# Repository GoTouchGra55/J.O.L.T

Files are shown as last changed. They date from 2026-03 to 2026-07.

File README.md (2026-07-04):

# 🚧 Under Active Development 🚧

# J.O.L.T ⚡

## Overview

JOLT (short for Joint Operated Legged Terrain walker) is my attempt at making a 12-DOF quadruped robot from scratch.

Yes, I designed a custom STM32-based dev board, CAD, and will implement custom firmware! :3

---

### PCB Design (2-layer)

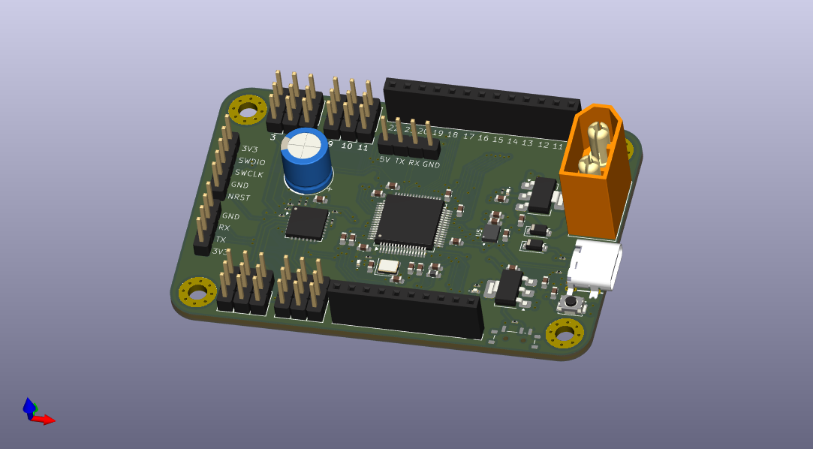
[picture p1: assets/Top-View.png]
PCB Top


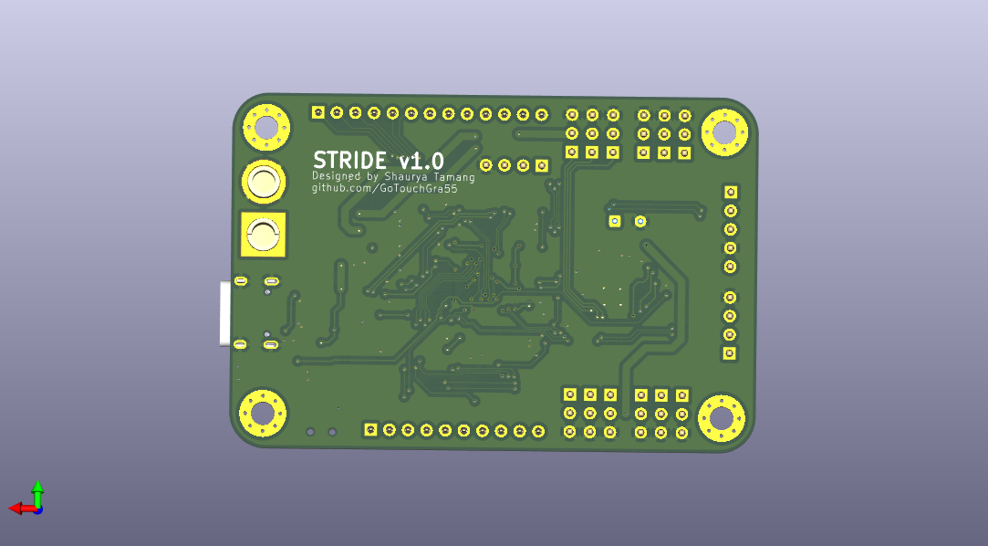
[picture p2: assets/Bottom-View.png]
PCB Bottom


#### Routing

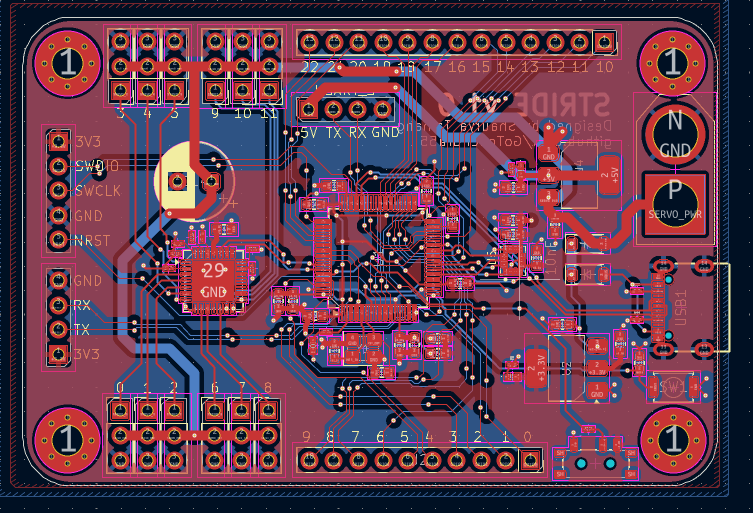
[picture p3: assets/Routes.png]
PCB Routes


### Schematics

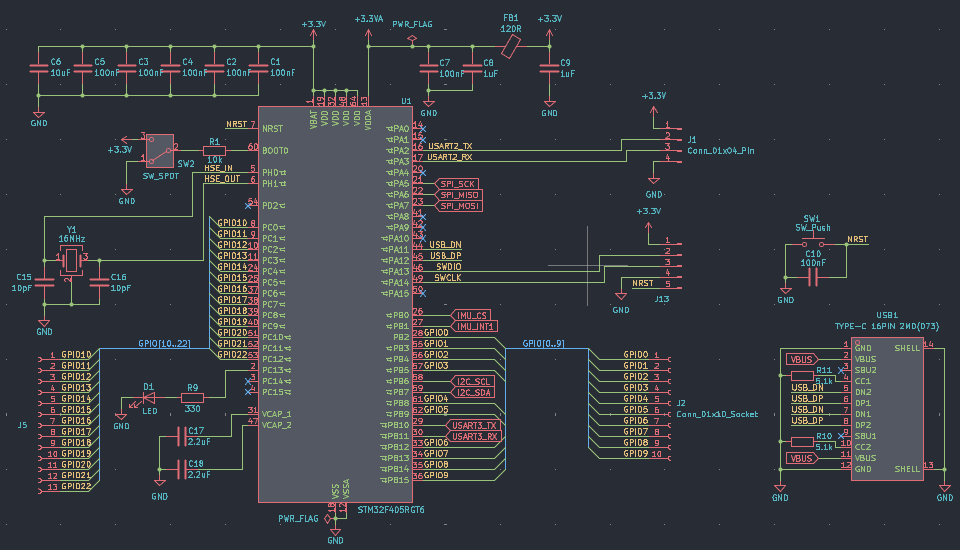
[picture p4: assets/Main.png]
MAIN schematic


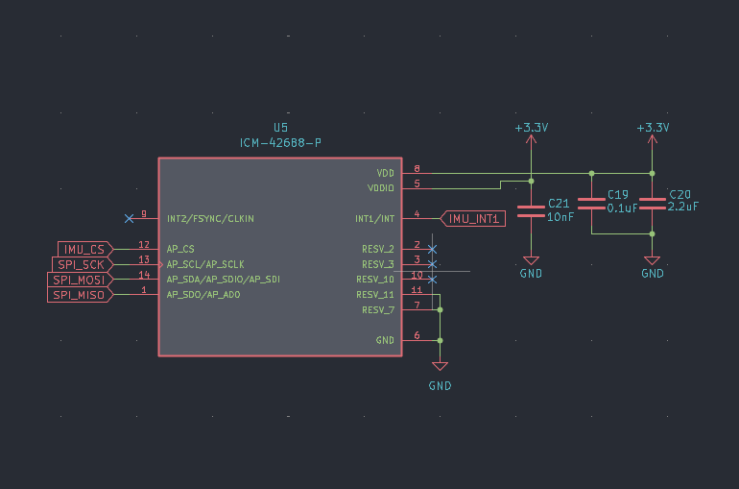
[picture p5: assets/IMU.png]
IMU schematic


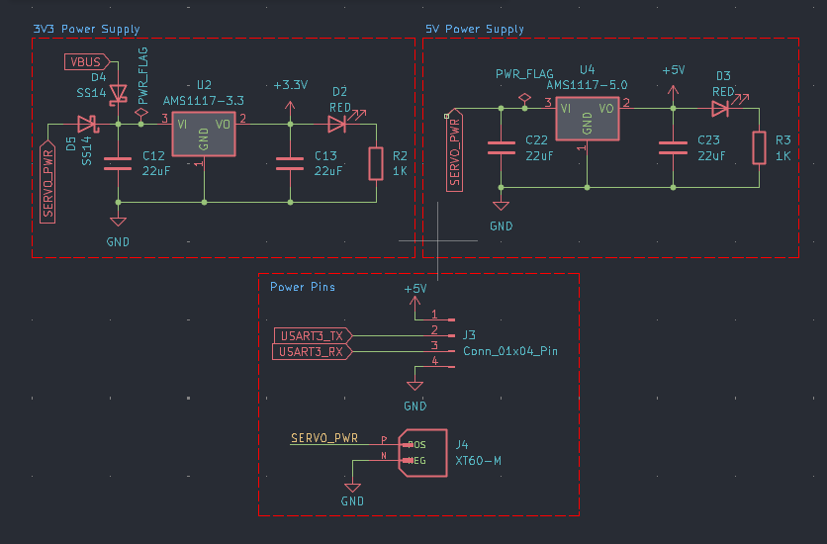
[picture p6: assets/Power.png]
POWER schematic


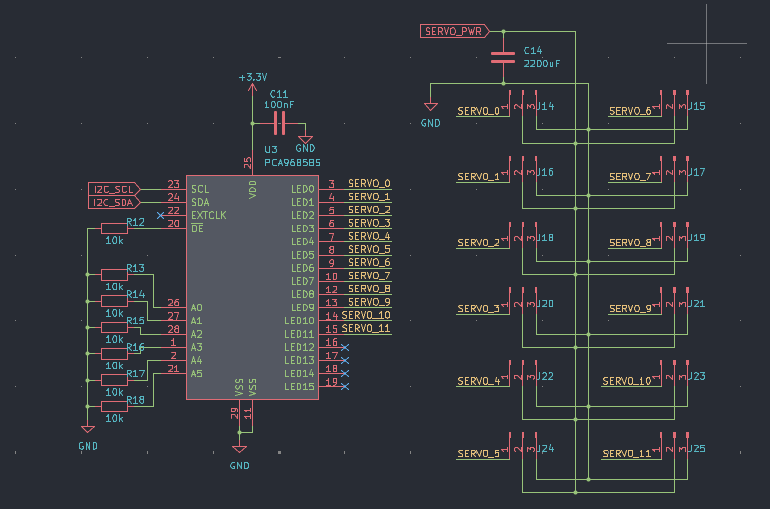
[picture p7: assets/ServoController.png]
Servo controller schematic


### Mechanical Design

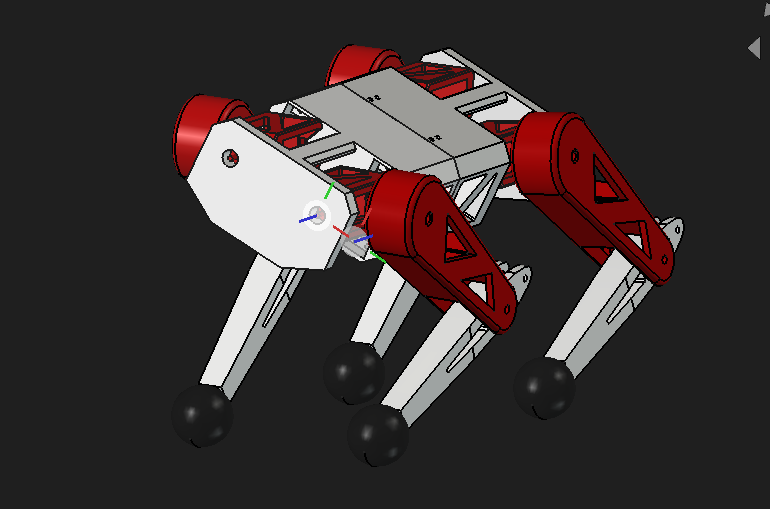
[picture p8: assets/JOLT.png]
JOLT CAD


Btw you might be wondering why there are so many triangular cutouts in the design.
Well first of all, it looks cool and secondly, I read an article about why triangles = **strong**.
I won't bother explaining the physics here but, you can do your own research on why that is.

*For those interested in the engineering principles, you can read more about why this geometry is superior for weight-to-strength ratios here: 
https://www.youtube.com/watch?v=Hn_iozUo9m4*

.stl files can be found at Print_Files

---

## System Architecture

### Power System

2s LiPo input (7.4V nominal voltage) is regulated to 5V and 3.3V rails for logic and peripherals.

Definitely don't use a higher cell lipo (unless you want to witness the magic smoke :p).

### Control System

An STM32F405RGT6 MCU handles the math and motion control while a PCA9685 PWM servo controller chip controls all 12 servos across 4 legs.

### Sensing

An onboard IMU provides orientation and motion feedback.

---

## Hardware

### Actuators

| Joint | Servo  | Count |
| --- | --- | ----- |
| Hip yaw | MG996R | 4 |
| Hip pitch | MG996R | 4 |
| Knee | MG996R | 4 |

---

### Development Board

| Component | Part |
| --- | --- |
| MCU | STM32F405RGT6 |
| IMU | ICM42688-P |
| Servo Driver | PCA9685BS |
| Power | 5V + 3.3V LDO |
| Debug | ST-Link v2 |
| Input | XT-60 (2s LiPo) |

## Assembly Guide

### Electronics

Unless you want a _not so pleasant_ experience, I'd advise you to follow the order below:

1. Solder all SMD components first (MCU, IMU, passives)
2. Solder larger components (connectors, headers)
3. Verify power rails (5V, 3.3V) before powering MCU
4. Flash firmware via ST-Link
5. Connect servos and test individual joints

### Body

1. Check parts for any sign of damage. Damaged part = Sad quadruped :(
2. Insert each servo into its respective slot and screw with suitable screws.
3. Make wiring as untangled as possible (because everyone likes cable management, right?)

---

## ⚠️ Warning

1. Double-check polarity of capacitors and power input before powering the board. Otherwise you've made a fancy capacitor bomb :D
2. Use a 2s LiPo battery to ensure safety of components
3. **DO NOT** expose the LiPo battery to high heat or poke the cells.

---

## Firmware

In progress...

---

## Project Status

- [x] CAD
- [x] PCB
- [ ] Assembly
- [ ] Initial tests

---

## Bill of Materials

| Name | Purpose | Quantity | Total Cost (USD) | Distributor |
|---|---|---:|---:|---|
| Brass inserts | To secure the screws | 1 | 4.21 | Daraz Nepal |
| Metal Servo Horns | To connect servo with the linkages | 2 | 18.35 | Daraz Nepal |
| Bearings | To ensure smooth movement | 1 | 5.47 | Daraz Nepal |
| 0603 Resistors | Used in circuit | 1 | 4.58 | Daraz Nepal |
| Devboard PCB | The brains and the body of the quadruped | 1 | 135.41 | JLCPCB |
| Female Header Pins | For GPIO pins | 1 | 0.71 | Daraz Nepal |
| XT-60 Connector | To connect the battery to the board | 1 | 0.54 | Daraz Nepal |
| M4 Screws | To secure the components | 1 | 3.96 | Daraz Nepal |
| MG996R Servos | To move the joints of the robot | 12 | 41.08 | Daraz Nepal |
| Capacitor | Used in circuit | 1 | 0.65 | Daraz Nepal |
| Tweezers | To hold tiny 0201 components | 1 | 2.62 | Daraz Nepal |
| Solder Paste | For soldering | 1 | 4.26 | Daraz Nepal |
| Shipping | Shipping costs | 1 | 26.81 | Daraz Nepal + JLCPCB |
| **Total** |  |  | **248.65** |  |

---

## License

MIT License - see [LICENSE](LICENSE)

---

## Author

**Shaurya Tamang**  
GitHub: https://github.com/GoTouchGra55  
Website: https://shauryatamang.netlify.app

---

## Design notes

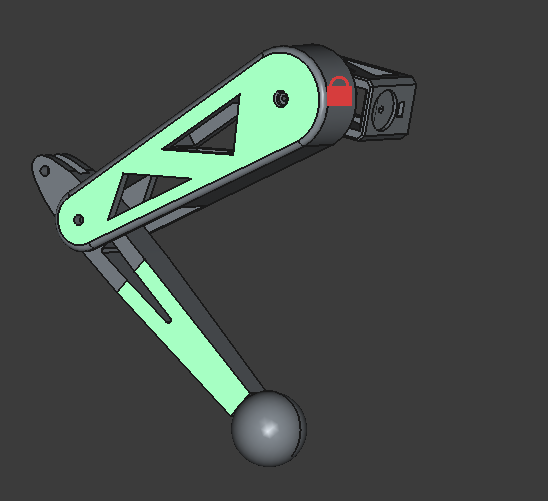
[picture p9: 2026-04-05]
assets/Leg.png

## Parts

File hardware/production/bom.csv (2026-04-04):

Designator | Footprint | Quantity | Value | LCSC Part #
0, 1, 10, 11, 2, 3, 4, 5, 6, 7, 8, 9 | PinHeader_1x03_P2.54mm_Vertical | 12 | Conn_01x03_Pin
C1, C10, C11, C2, C3, C4, C5, C7 | 0603 | 8 | 100nF
C12, C13, C22, C23 | 0603 | 4 | 22uF
C14 | CP_Radial_D8.0mm_P3.50mm | 1 | 2200uF
C15, C16 | 0603 | 2 | 10pF
C17, C18, C20 | 0603 | 3 | 2.2uF
C19 | 0603 | 1 | 0.1uF
C21 | 0603 | 1 | 10nF
C6 | 0603 | 1 | 10uF
C8, C9 | 0603 | 2 | 1uF
D1 | 0402 | 1 | LED
D2, D3 | 0402 | 2 | RED
D4, D5 | D_SOD-123 | 2 | SS14
FB1 | 0603 | 1 | 120R
J1, J3 | PinHeader_1x04_P2.54mm_Vertical | 2 | Conn_01x04_Pin
J13 | PinHeader_1x05_P2.54mm_Vertical | 1 | Conn_01x05_Pin
J2 | PinSocket_1x10_P2.54mm_Vertical | 1 | Conn_01x10_Socket
J4 | AMASS_XT60-M | 1 | XT60-M
J5 | PinSocket_1x13_P2.54mm_Vertical | 1 | Conn_01x13_Socket
R1, R12, R13, R14, R15, R16, R17, R18 | 0201 | 8 | 10k
R10, R11 | 0201 | 2 | 5.1k
R2, R3 | 0201 | 2 | 1K
R9 | 0201 | 1 | 330
SW1 | SW_Push_SPST_NO_Alps_SKRK | 1 | SW_Push
SW2 | SW_SPDT_Shouhan_MSK12C02 | 1 | SW_SPDT
U1 | LQFP-64_10x10mm_P0.5mm | 1 | STM32F405RGT6
U2 | SOT-223-3_TabPin2 | 1 | AMS1117-3.3
U3 | QFN-28-1EP_6x6mm_P0.65mm_EP4.25x4.25mm | 1 | PCA9685BS
U4 | SOT-223-3_TabPin2 | 1 | AMS1117-5.0
U5 | PQFN50P300X250X97-14N | 1 | ICM-42688-P
USB1 | USB-C-SMD_TYPE-C-6PIN-2MD-073 | 1 | TYPE-C 16PIN 2MD(073) | C2765186
Y1 | Crystal_SMD_3225-4Pin_3.2x2.5mm | 1 | 16MHz

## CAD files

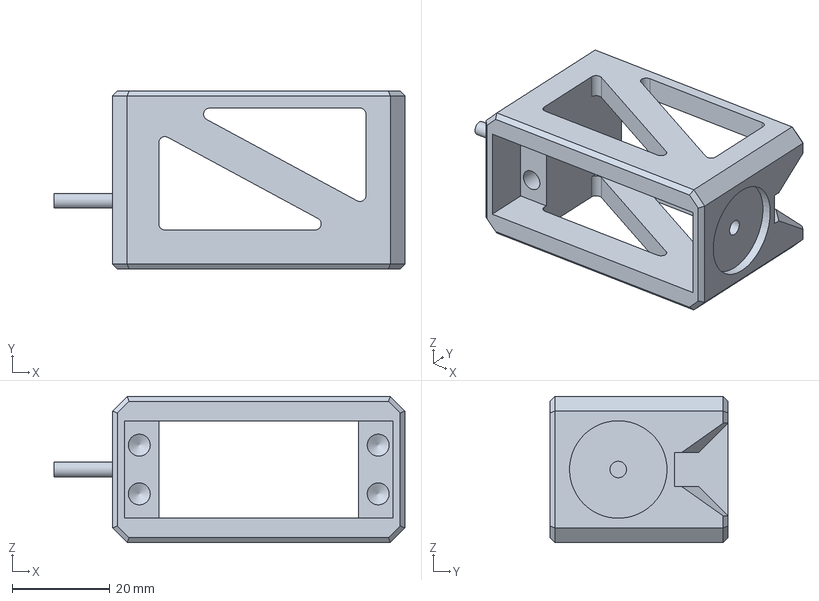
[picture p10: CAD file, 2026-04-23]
hardware/FreeCAD_files/JOLT_HIP.FCStd
72.0 x 36.5 x 30.0 mm

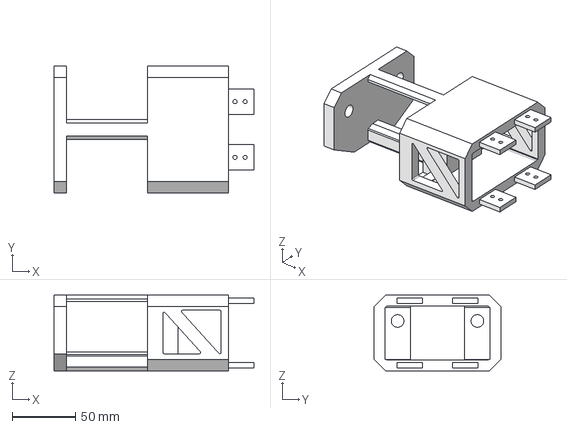
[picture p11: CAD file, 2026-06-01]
hardware/Print_Files/JOLT_Chassis_Pin-Body.step
158.0 x 100.0 x 60.0 mm

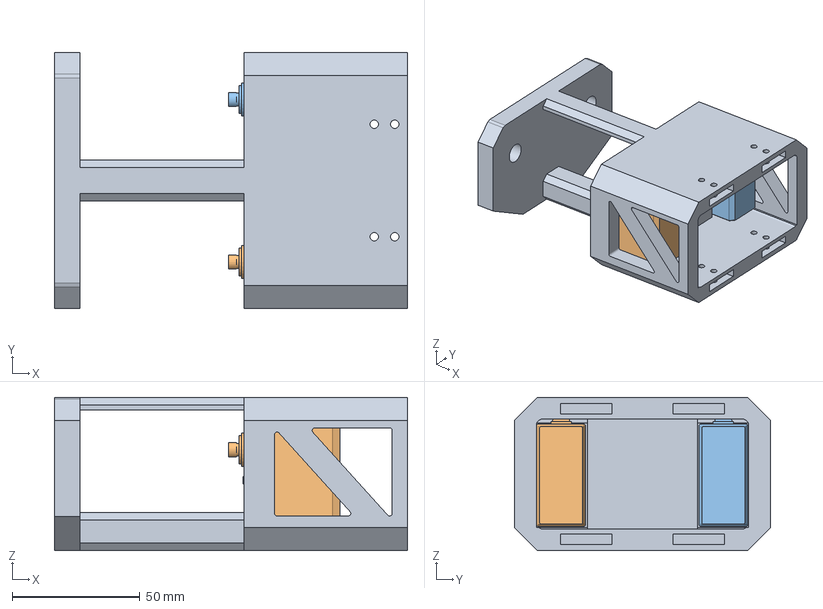
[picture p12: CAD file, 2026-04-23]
hardware/FreeCAD_files/JOLT_Chassis_Socket.FCStd
138.0 x 100.0 x 60.0 mm
MG996R_Servo_Model
MG996R_Servo_Model001

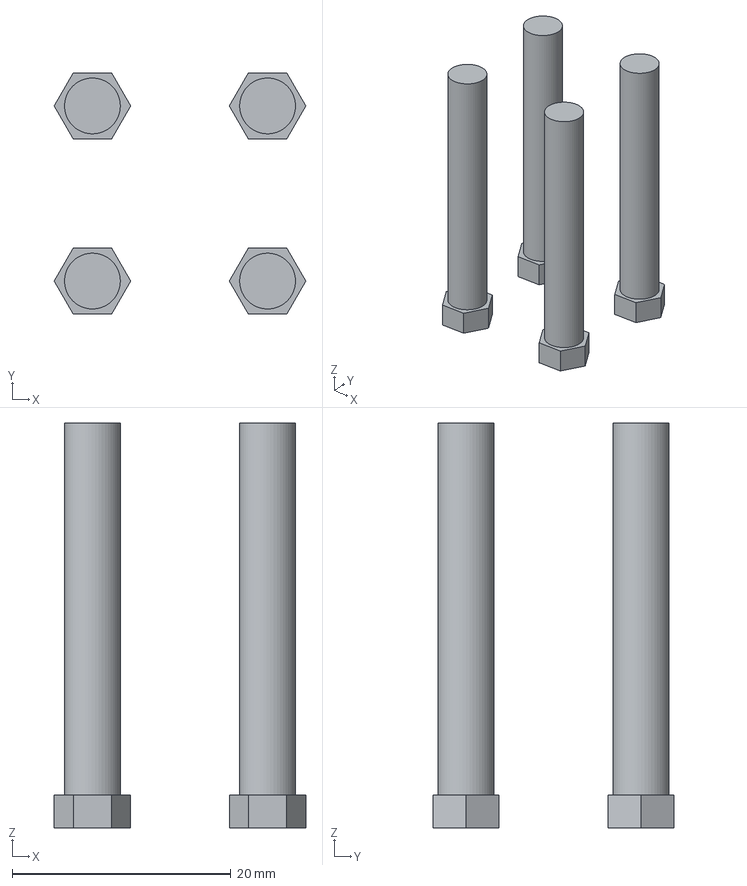
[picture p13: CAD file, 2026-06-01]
hardware/Print_Files/JOLT_Misc-Body.step
23.0 x 22.1 x 37.0 mm

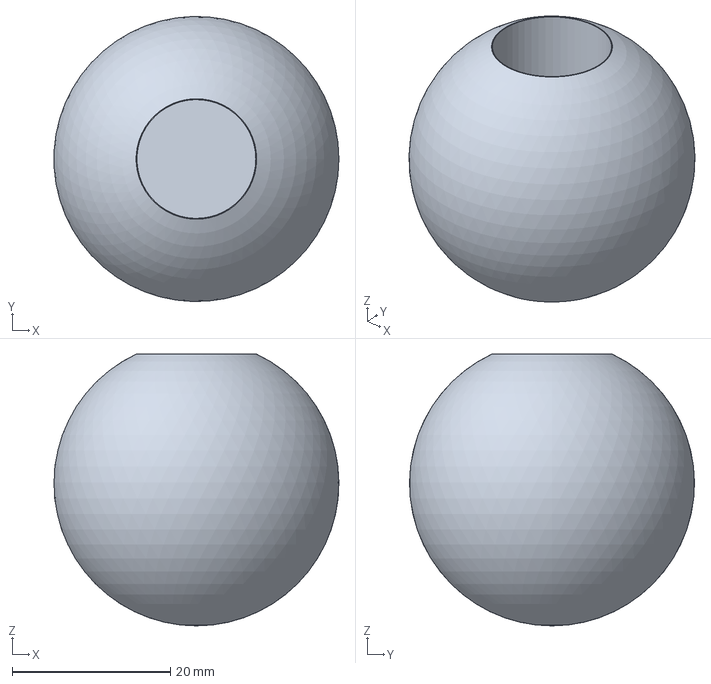
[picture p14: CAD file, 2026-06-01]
hardware/Print_Files/JOLT_GRIP-Cut.step
36.0 x 36.0 x 34.3 mm

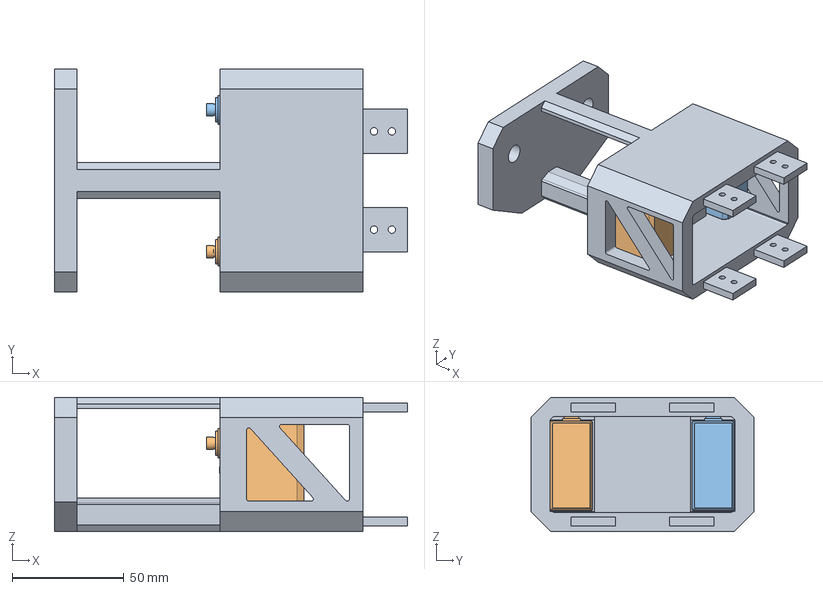
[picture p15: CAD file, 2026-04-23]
hardware/FreeCAD_files/JOLT_Chassis_Pin.FCStd
158.0 x 100.0 x 60.0 mm
MG996R_Servo_Model
MG996R_Servo_Model001

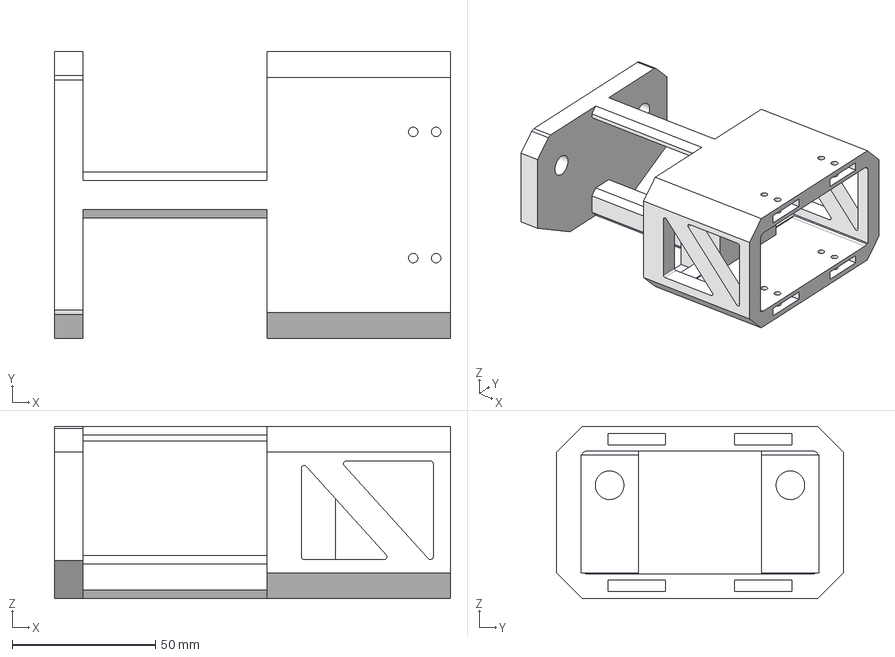
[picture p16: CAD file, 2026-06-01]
hardware/Print_Files/JOLT_Chassis_Socket-Body.step
138.0 x 100.0 x 60.0 mm

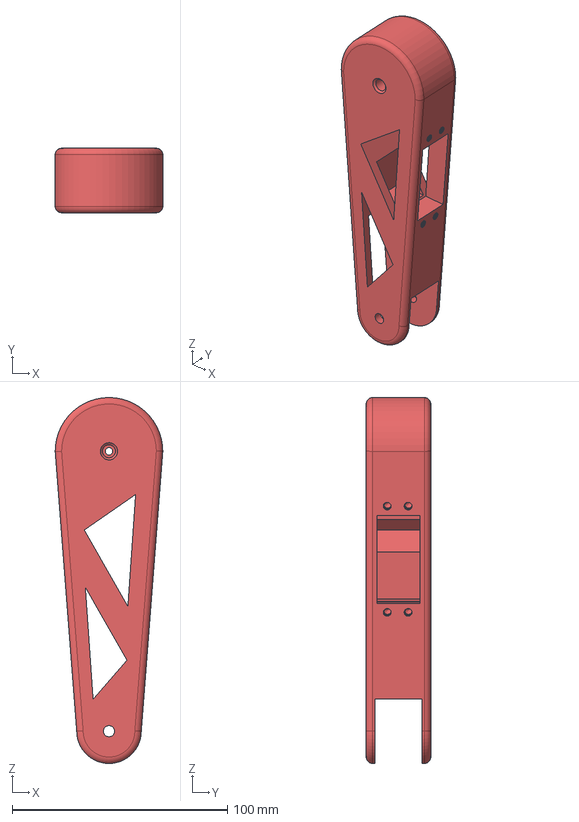
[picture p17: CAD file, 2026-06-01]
hardware/Print_Files/JOLT_Femur_LEFT-Body.step
50.0 x 30.0 x 170.0 mm

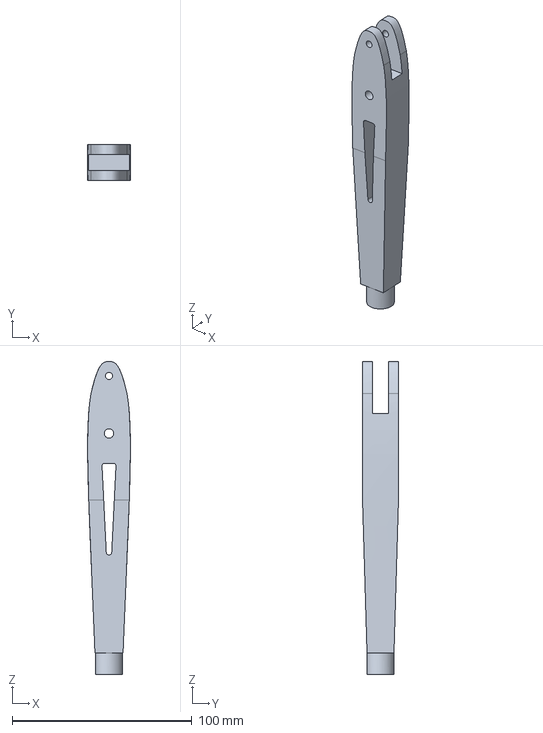
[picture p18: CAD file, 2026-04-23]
hardware/FreeCAD_files/JOLT_Tibia.FCStd
23.8 x 20.0 x 174.0 mm

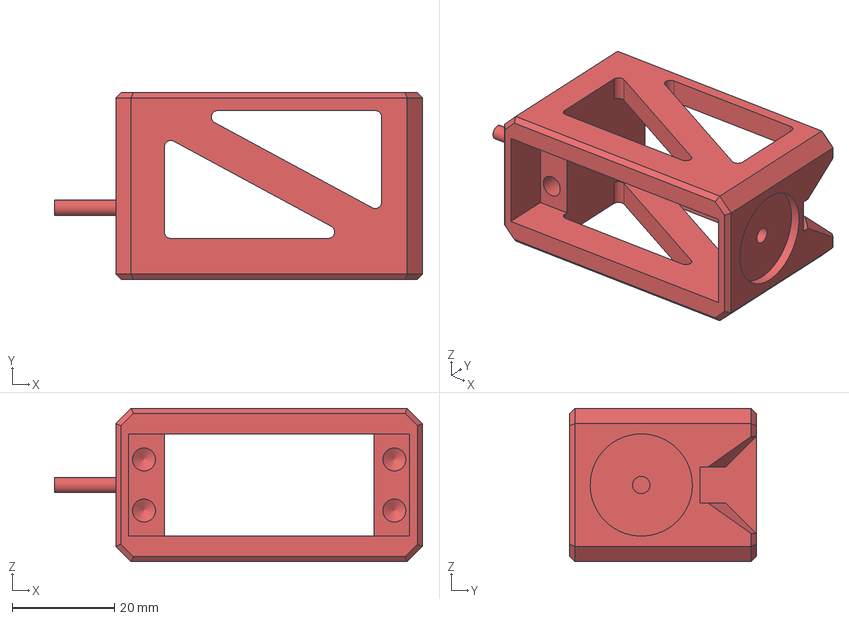
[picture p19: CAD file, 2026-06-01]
hardware/Print_Files/JOLT_HIP-Body.step
72.0 x 36.5 x 30.0 mm

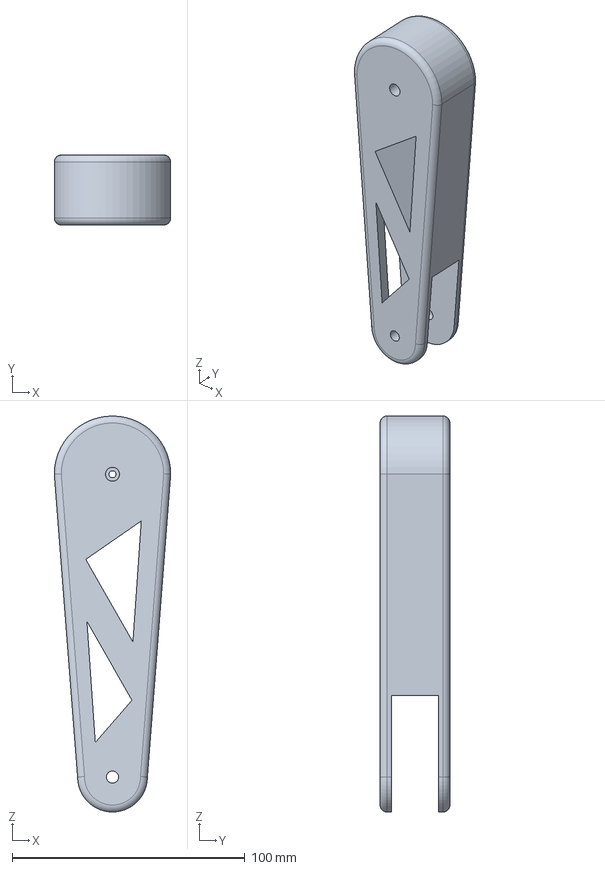
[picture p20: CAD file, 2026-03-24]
hardware/FreeCAD_files/JOLT_Femur.FCStd
50.0 x 30.0 x 170.0 mm

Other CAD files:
hardware/FreeCAD_files/JOLT_Assembled.FCStd
hardware/FreeCAD_files/JOLT_GRIP.FCStd
hardware/FreeCAD_files/JOLT_Femur_LEFT.FCStd
hardware/Print_Files/JOLT_Femur_RIGHT-Body.step
hardware/Print_Files/JOLT_Tibia-Body.step
hardware/FreeCAD_files/JOLT_Femur_RIGHT.FCStd
hardware/Print_Files/JOLT_Chassis_Pin-Body.stl
hardware/Print_Files/JOLT_Chassis_Socket-Body.stl
hardware/Print_Files/JOLT_Femur_LEFT-Body.stl
hardware/Print_Files/JOLT_Femur_RIGHT-Body.stl
hardware/Print_Files/JOLT_GRIP-Cut.stl
hardware/Print_Files/JOLT_HIP-Body.stl
hardware/Print_Files/JOLT_Misc-Body.stl
hardware/Print_Files/JOLT_Tibia-Body.stl

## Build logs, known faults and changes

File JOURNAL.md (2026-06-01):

<!--
  This journal is auto generated by Stasis.
-->

# 4/23/2026 8 AM - Chassis design

_Time spent: 3h_

After I came to know that a guy from printing legion actually ships to my location, I made the chassis design too! Note that this was made a few days prior to the recent feedback.

Since the print bed couldn't fit my original chassis design, I separated it into two parts (Socket and Pin) which are screwed together.

I will be updating my README file now.

Screenshot from 2026-04-21 21-43-59

Screenshot from 2026-04-21 21-43-47

Screenshot from 2026-04-21 21-43-37

# 4/18/2026 5 AM - Reworking some components!

_Time spent: 1h_

So, I spent an hour moving the back copper compnents to the front plate according to my reviewer. It definitely looks a bit cluttered, but anything to save costs!

Thats all. i don't really have much to say. I'll probably just redo the readme file too.

Screenshot from 2026-04-18 10-43-19

Screenshot from 2026-04-18 10-43-28

Screenshot from 2026-04-18 10-43-37

# 4/5/2026 9 AM - Cleanup

_Time spent: 1h_

I added some silkscreen text for board description on the back silkscreen layer and also GPIO numbering for convienience and made some minor routing adjustments. But other than that, the design phase is over. Yay!

Screenshot from 2026-04-05 14-22-29

Screenshot from 2026-04-05 14-22-15

# 4/4/2026 3 PM - Finish

_Time spent: 5.5h_

After a couple of weeks of work, I can finally say that JOLT is COMPLETE! (atleast in theory) now I can work on other projects and enhance my skills!

Screenshot from 2026-04-04 21-13-22

I basically had to re-route some previous routes to make way for the newer routes and also had to edit some default footprints but other than that, I've learned my lesson. That is, to use more layers for complex projects.

Screenshot from 2026-04-04 21-11-47

Screenshot from 2026-04-04 21-11-35

# 4/3/2026 5 PM - Routing

_Time spent: 4h_

Can't believe that I managed to make the routing prettier than I anticipated. I forgot to rotate the servo pins on the opposite side yesterday. So, I did that and had to re-route the entire thing. Anyways, I'm going to finish the routing today and hopefully submit tomorrow!

Screenshot from 2026-04-03 23-07-05

Screenshot from 2026-04-02 21-40-33

Screenshot from 2026-04-03 23-17-51

# 4/2/2026 4 PM - Routing

_Time spent: 1h_

I'm happy with the progress I made within an hour. Since this is my first custom devboard, its probably not gonna look the prettiest or even have the prettiest routing (It already looks horrendous). But at the end of the day, everyone starts somewhere ig. Anyways, I'm targetting the finish date as tomorrow for the pcb so yay! Oh and I kept the USART3 pins closer to the stm32 chip because it will serve as my radio receiver for this project. The other USART pins are kept at the edges since they're not very useful except the flashing pins.

Screenshot from 2026-04-02 21-40-33

Screenshot from 2026-04-02 21-40-24

Screenshot from 2026-04-02 21-39-07

# 4/2/2026 1 PM - PCB design and routing

_Time spent: 3h_

Spent a solid few hours coming up with the design. Went through two iterations and I'm happy with this design. I should probably add 4 mounting holes instead of the current 2. So I'll probably make space to do it. Either way, I estimate the completion of this project within 2 days. Going back to work!

Screenshot from 2026-04-02 19-36-14

Screenshot from 2026-04-02 19-33-17

Screenshot from 2026-04-02 19-33-09

# 4/1/2026 11 AM - Schematic Finish and Footprint Assignment

_Time spent: 3h_

I finally finished the schematics after a couple of days of work! Also assigned the footprints. I added some bounding boxes on the power schematics but didnt on other bc I was pretty lazy to do it. GOsh the erc errors went crazy because I placed local labels instead of global ones despite using multiple sheets but it was a quick fix!

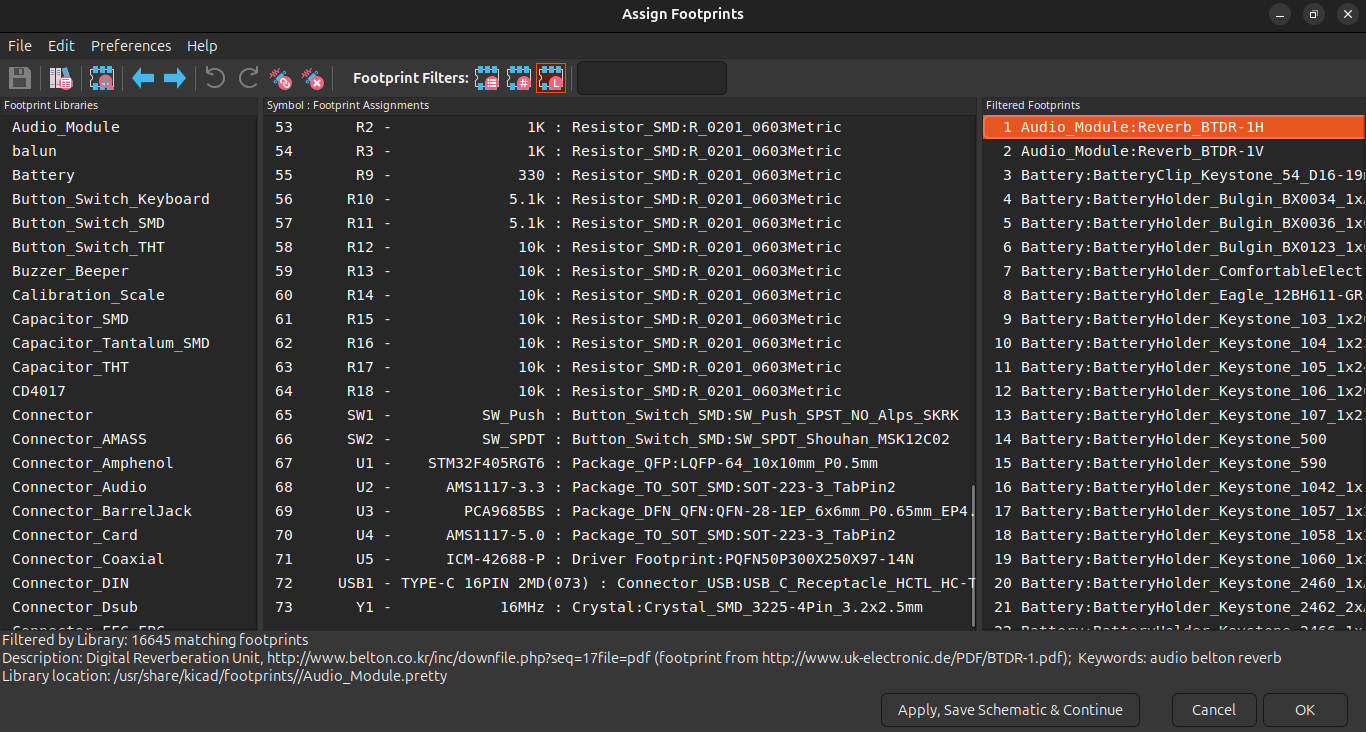
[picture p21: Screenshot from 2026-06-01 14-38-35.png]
Footprint


# 3/31/2026 3 PM - Schematics

_Time spent: 4.333333333333333h_

I just cleaned up the schematics and also divided the file into 3 separate files. I also added a voltage regulator and bus connection to make the connections neat.

Screenshot from 2026-03-31 22-06-48

Screenshot from 2026-03-31 21-31-45

Screenshot from 2026-03-31 21-31-36

# 3/30/2026 4 PM - Schematics

_Time spent: 3h_

I read through the official stm32 guidelines and wired up the crystal, usb-c port and also the pca9685 chip (Pwm servo driver).

Screenshot from 2026-03-30 21-09-20

Screenshot from 2026-03-30 21-51-49

Screenshot from 2026-03-30 21-51-37

Currently, I've only connected the pca9685 chip and tomorrow I'll be adding the PDU (Power Distribution Unit).

# 3/29/2026 3 PM - Schematics

_Time spent: 1h_

I havent really been able to spend much time on stasis due to personal reasons but I hope to dedicate more time from tomorrow onwards. Anyways, I mapped out all the pins from the STM32 CubeMX software and also wired up the icm42688p chip. I learned that I could find the wiring structures by reading through the component docs!

Screenshot from 2026-03-29 21-36-55

Screenshot from 2026-03-29 21-37-01

# 3/28/2026 2 PM - Micro-controller pinout mapping

_Time spent: 0.75h_

I learned to use the stm32 cubemx software to map out the pins for the stuff I'll be doing with the mcu! Here I mapped out the i2c, spi, usb and a crystal oscillator.

Screenshot from 2026-03-28 20-20-27

Screenshot from 2026-03-28 20-20-20

# 3/25/2026 1 PM - Chassis design and finalization

_Time spent: 3.25h_

I was halfway through designing the chassis when I suddenly realized that I had a toy engineering set from when I was little. The 3d printed chassis would go out of budget so I decided to use that playset to create the chassis! But here's the incomplete chassis which I'll sadly no longer continue.

Screenshot from 2026-03-25 19-25-35

Screenshot from 2026-03-25 19-25-31

# 3/24/2026 1 PM - Hip Bracket

_Time spent: 2.5h_

After a lot of iterations, I finally present to you the HIP bracket! I pocketed out triangles because they are strong and also reduce printing costs. I also removed the screw threading since it was lagging my system a lot. But overall, I'm happy with how it turned out :). Only the chassis remains before I start work on the custom devboard!

Screenshot from 2026-03-24 19-16-28

Screenshot from 2026-03-24 19-16-09

# 3/23/2026 11 AM - Finish Legs

_Time spent: 3.25h_

I finally finished the legs (Had to redo the files I deleted yesterday!). It turned out pretty nice for a newbie like me. Honestly, I didnt expect it to look this good. Damn remaking the files does take a long amount of time. 

Screenshot from 2026-03-23 17-08-31

I'm gonna start the work on the hip brackets now.

Screenshot from 2026-03-23 20-48-13

# 3/22/2026 3 PM - Design iteration #4

_Time spent: 2.75h_

So, I just found out that my designed 3d parts would easily eat through the $300 budget.
Screenshot from 2026-03-22 18-25-28

But if I remove the grips and the tibia, the cost is greatly reduced.
Screenshot from 2026-03-22 18-25-17

So I decided to go with this sort of leg design (Credit: [Aaed Musa](https://www.youtube.com/watch?v=VhUvoV5XyRg)) where I would 3d print the femur but for the tibia I'd use black markers as they're cheap, light-weight, and strong.

Screenshot from 2026-03-22 18-19-25

Screenshot from 2026-03-22 20-55-23

P.S: An employee just told me that I can split the project into two separate ones if it met the required complexity. I REGRET DELETING THE OG FILE. Thankfully I have my tibia file. But just give me a break. I'm done for the day. Not working anymore (;-;)

# 3/21/2026 4 PM - Femur Refinements

_Time spent: 1.25h_

Just finished refining the femur. I think it looks really nice. I had to pocket out the bottom part of the femur for clearance reasons since I'm not using the [clevis joint](https://en.wikipedia.org/wiki/Clevis_fastener). Not much to elaborate here.

Screenshot from 2026-03-21 21-49-23

Everything is just working out soo quick after I finalized the femur design. Anyways, I'll carve out custom servo mounts tomorrow. I need to sleep now (I have school tomorrow)

Screenshot from 2026-03-21 21-33-57

Screenshot from 2026-03-21 20-15-14

# 3/21/2026 2 PM - Femur design

_Time spent: 3.75h_

AFTER 4 DESIGN ITERATIONS, FINALLY I DID THE FEMUR! Still need to make spaces for the linkages and pivots.
Took some inspiration from other robot dogs on youtube but I think this looks pretty neat. The first 2 were pretty much just disastrous bc I tried to make a femur with one of those long linkages rolling on top to move the tibia, but after the 3rd iteration, I thought that a simpler system would be so much better since this does not really use any fancy brushless motors. 

Screenshot from 2026-03-21 20-15-14

Screenshot from 2026-03-21 20-15-10

P.S: I forgot to take the screenshots of previous iterations (Forgive me)

# 3/20/2026 10 AM - Tibia Final

_Time spent: 1h_

Finally finished the tibia. Didn't really use datum planes since, I still do not know how to use it; but I learned a different trick! That is to make a sketch on a normal plane and then translate it to a specific coordinate in space THEN use the pocket operation to remove material from curved surfaces.

Screenshot from 2026-03-20 16-13-12

Now I'll start work on the femur.

Screenshot from 2026-03-20 16-13-08

# 3/20/2026 8 AM - Design iteration #3

_Time spent: 2h_

Ok I promise this is the last time that I'll touch the tibia design. Decided to go minimalistic. Just learning datum planes to make the thickness more dynamic. Man freecad is a pain in the bum. Ig I should just switch to onshape. But ehh I'll just stick to this painful software for now.

Screenshot from 2026-03-20 14-32-47

Screenshot from 2026-03-20 14-32-39

# 3/19/2026 4 PM - Tibia Redesign

_Time spent: 2h_

I redesigned the tibia to a simpler version (for safety reasons as I'm a beginner to cad). The rest is pretty much the same. I cant believe I spent this long redesigning a stupid leg. It's partly because I was busy fighting freecad errors tho-

Screenshot from 2026-03-19 21-46-54
Screenshot from 2026-03-19 21-46-42

# 3/19/2026 9 AM - CAD

_Time spent: 2h_

Took some inspiration from the MIT Cheetah Quadruped. I really liked its sleek aesthetics.

Also added triangles because they are strong and also look super cool (also partly because they'll reduce the overall weight and cost). I also think that this makes it seems like an actual cheetah's leg due to the sleekness.

Screenshot from 2026-03-19 15-13-14

Screenshot from 2026-03-19 14-55-38

# 3/18/2026 2 PM - Test Rig Fix

_Time spent: 0.2h_

I thought nothing of it first but upon testing out the test rig, I realized that I accidentally fixed the movement to only a single axis! (my bad) So I quickly fixed the error





# 3/18/2026 1 PM - Test frame and design finalization

_Time spent: 1.75h_

I just did the inverse kinematic equations and made a test frame using some spare mg995 servos that I had from a previous project. Also the design finalization took wayy too long. I'm gonna start work on the CAD now.



Decided to go with a parallel linkage as it makes the robot legs less bulky and also looks pretty cool imo. This one is definitely the final design



# 3/17/2026 1 PM - Hardware research and approximations

_Time spent: 1h_

So, I decided to go on with a hybrid servo approach consisting of 4 35kg/cm servos for critical joint sections and 8 ~10kg/cm ones for the less critical parts to optimize cost and efficiency.

Screenshot from 2026-03-17 15-29-52

Screenshot from 2026-03-17 15-27-44

Also did all the weight calculations and finalized the link lengths.



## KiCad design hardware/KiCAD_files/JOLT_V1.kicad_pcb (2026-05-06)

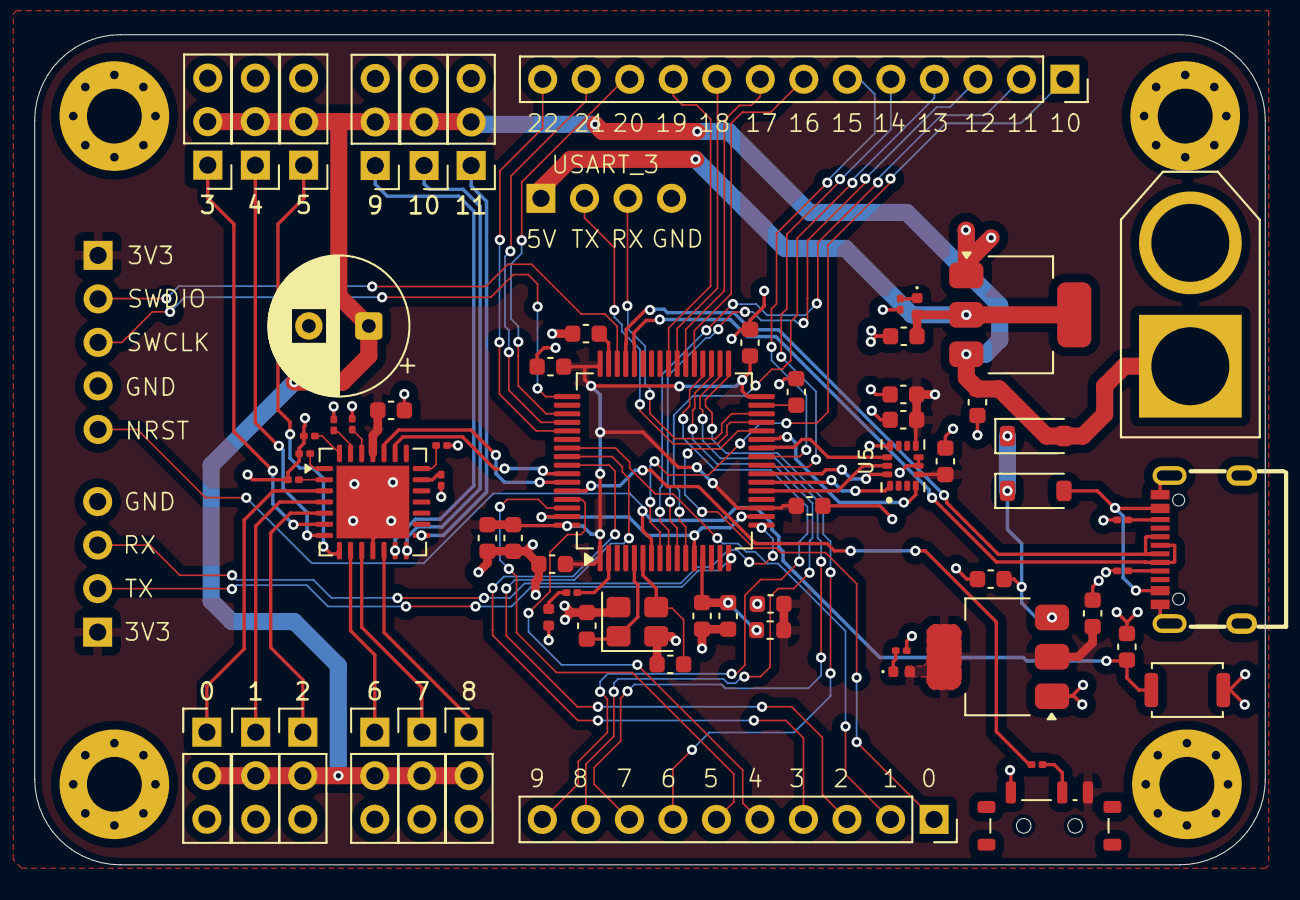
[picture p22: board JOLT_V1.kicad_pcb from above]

Board: 2 copper layers, 71.8 x 48.5 mm, 73 parts (0 on the bottom side), 77 nets.

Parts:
0, 1, 2, 3, 4, 5, 6, 7, 8, 9, 10, 11: Conn_01x03_Pin; PinHeader_1x03_P2.54mm_Vertical
C1, C2, C3, C4, C5, C7, C10, C11: 100nF; C_0603_1608Metric
C6: 10uF; C_0603_1608Metric
C8, C9: 1uF; C_0603_1608Metric
C12, C13, C22, C23: 22uF; C_0603_1608Metric
C14: 2200uF; CP_Radial_D8.0mm_P3.50mm
C15, C16: 10pF; C_0603_1608Metric
C17, C18, C20: 2.2uF; C_0603_1608Metric
C19: 0.1uF; C_0603_1608Metric
C21: 10nF; C_0603_1608Metric
D1: LED; LED_0402_1005Metric
D2, D3: RED; LED_0402_1005Metric
D4, D5: SS14; D_SOD-123
FB1: 120R; L_0603_1608Metric
H1, H2, H3, H4: MountingHole_3.2mm_M3_Pad_Via
J1, J3: Conn_01x04_Pin; PinHeader_1x04_P2.54mm_Vertical
J2: Conn_01x10_Socket; PinSocket_1x10_P2.54mm_Vertical
J4: XT60-M; AMASS_XT60-M
J5: Conn_01x13_Socket; PinSocket_1x13_P2.54mm_Vertical
J13: Conn_01x05_Pin; PinHeader_1x05_P2.54mm_Vertical
R1, R12, R13, R14, R15, R16, R17, R18: 10k; R_0201_0603Metric
R2, R3: 1K; R_0201_0603Metric
R9: 330; R_0201_0603Metric
R10, R11: 5.1k; R_0201_0603Metric
SW1: SW_Push; SW_Push_SPST_NO_Alps_SKRK
SW2: SW_SPDT; SW_SPDT_Shouhan_MSK12C02
U1: STM32F405RGT6; LQFP-64_10x10mm_P0.5mm
U2: AMS1117-3.3; SOT-223-3_TabPin2
U3: PCA9685BS; QFN-28-1EP_6x6mm_P0.65mm_EP4.25x4.25mm
U4: AMS1117-5.0; SOT-223-3_TabPin2
U5: ICM-42688-P; PQFN50P300X250X97-14N
USB1: TYPE-C 16PIN 2MD(073); USB-C-SMD_TYPE-C-6PIN-2MD-073
Y1: 16MHz; Crystal_SMD_3225-4Pin_3.2x2.5mm

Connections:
+3.3V: C1.1, C2.1, C3.1, C4.1, C5.1, C6.1, C9.1, C11.1, C13.1, C19.1, C20.1, C21.1, D2.2 (A), FB1.2, J1.1, J13.1, SW2.3 (C), U1.1 (VBAT), U1.19 (VDD), U1.32 (VDD), U1.48 (VDD), U1.64 (VDD), U2.2 (VO), U3.25 (VDD), U5.5 (VDDIO), U5.8 (VDD)
+3.3VA: C7.1, C8.1, FB1.1, U1.13 (VDDA)
+5V: C23.1, D3.2 (A), J3.1, U4.2 (VO)
/Main/GPIO0: J2.1, U1.28 (PB2)
/Main/GPIO1: J2.2, U1.55 (PB3)
/Main/GPIO2: J2.3, U1.56 (PB4)
/Main/GPIO3: J2.4, U1.57 (PB5)
/Main/GPIO4: J2.5, U1.61 (PB8)
/Main/GPIO5: J2.6, U1.62 (PB9)
/Main/GPIO6: J2.7, U1.33 (PB12)
/Main/GPIO7: J2.8, U1.34 (PB13)
/Main/GPIO8: J2.9, U1.35 (PB14)
/Main/GPIO9: J2.10, U1.36 (PB15)
/Main/GPIO10: J5.1, U1.8 (PC0)
/Main/GPIO11: J5.2, U1.9 (PC1)
/Main/GPIO12: J5.3, U1.10 (PC2)
/Main/GPIO13: J5.4, U1.11 (PC3)
/Main/GPIO14: J5.5, U1.24 (PC4)
/Main/GPIO15: J5.6, U1.25 (PC5)
/Main/GPIO16: J5.7, U1.37 (PC6)
/Main/GPIO17: J5.8, U1.38 (PC7)
/Main/GPIO18: J5.9, U1.39 (PC8)
/Main/GPIO19: J5.10, U1.40 (PC9)
/Main/GPIO20: J5.11, U1.51 (PC10)
/Main/GPIO21: J5.12, U1.52 (PC11)
/Main/GPIO22: J5.13, U1.53 (PC12)
/Main/HSE_IN: C15.1, U1.5 (PH0), Y1.1
/Main/HSE_OUT: C16.1, U1.6 (PH1), Y1.3
/Main/NRST: C10.2, J13.5, SW1.2, U1.7 (NRST)
/Main/SWCLK: J13.3, U1.49 (PA14)
/Main/SWDIO: J13.2, U1.46 (PA13)
/Main/USART2_RX: J1.3, U1.17 (PA3)
/Main/USART2_TX: J1.2, U1.16 (PA2)
/Main/USB_DN: U1.44 (PA11), USB1.5 (DN2), USB1.7 (DN1)
/Main/USB_DP: U1.45 (PA12), USB1.6 (DP1), USB1.8 (DP2)
/Servo_Controller/SERVO_0: 0.1, U3.3 (LED0)
/Servo_Controller/SERVO_1: 1.1, U3.4 (LED1)
/Servo_Controller/SERVO_2: 2.1, U3.5 (LED2)
/Servo_Controller/SERVO_3: 3.1, U3.6 (LED3)
/Servo_Controller/SERVO_4: 4.1, U3.7 (LED4)
/Servo_Controller/SERVO_5: 5.1, U3.8 (LED5)
/Servo_Controller/SERVO_6: 6.1, U3.9 (LED6)
/Servo_Controller/SERVO_7: 7.1, U3.10 (LED7)
/Servo_Controller/SERVO_8: 8.1, U3.12 (LED8)
/Servo_Controller/SERVO_9: 9.1, U3.13 (LED9)
/Servo_Controller/SERVO_10: 10.1, U3.14 (LED10)
/Servo_Controller/SERVO_11: 11.1, U3.15 (LED11)
GND: 0.3, 1.3, 2.3, 3.3, 4.3, 5.3, 6.3, 7.3, 8.3, 9.3, 10.3, 11.3, C1.2, C2.2, C3.2, C4.2, C5.2, C6.2, C7.2, C8.2, C9.2, C10.1, C11.2, C12.2, C13.2, C14.2, C15.2, C16.2, C17.1, C18.1, C19.2, C20.2, C21.2, C22.2, C23.2, D1.1 (K), J1.4, J3.4, J4.N (NEG), J13.4, R2.2, R3.2, R10.1, R11.1, R12.2, R13.2, R14.2, R15.2, R16.2, R17.2, R18.2, SW1.1, SW2.1 (A), U1.12 (VSSA), U1.18 (VSS), U1.63 (VSS), U2.1 (GND), U3.11 (VSS), U3.29 (VSS), U4.1 (GND), U5.6 (GND), U5.7 (RESV_7), U5.11 (RESV_11), USB1.1 (GND), USB1.12 (GND), USB1.13 (SHELL), USB1.14 (SHELL), Y1.2 (G), Y1.4 (G)
I2C_SCL: U1.58 (PB6), U3.23 (SCL)
I2C_SDA: U1.59 (PB7), U3.24 (SDA)
IMU_CS: U1.26 (PB0), U5.12 (AP_CS)
IMU_INT1: U1.27 (PB1), U5.4 (INT1/INT)
unnamed: D1.2 (A), R9.1
unnamed: D2.1 (K), R2.1
unnamed: D3.1 (K), R3.1
unnamed: C12.1, D4.1 (K), D5.1 (K), U2.3 (VI)
unnamed: R1.1, SW2.2 (B)
unnamed: R1.2, U1.60 (BOOT0)
unnamed: R9.2, U1.2 (PC13)
unnamed: C17.2, U1.31 (VCAP_1)
unnamed: C18.2, U1.47 (VCAP_2)
unnamed: R13.1, U3.26 (A0)
unnamed: R14.1, U3.27 (A1)
unnamed: R15.1, U3.28 (A2)
unnamed: R16.1, U3.1 (A3)
unnamed: R17.1, U3.2 (A4)
unnamed: R18.1, U3.21 (A5)
unnamed: R12.1, U3.20 (~OE)
unnamed: R11.2, USB1.4 (CC1)
unnamed: R10.2, USB1.10 (CC2)
SERVO_PWR: 0.2, 1.2, 2.2, 3.2, 4.2, 5.2, 6.2, 7.2, 8.2, 9.2, 10.2, 11.2, C14.1, C22.1, D5.2 (A), J4.P (POS), U4.3 (VI)
SPI_MISO: U1.22 (PA6), U5.1 (AP_SDO/AP_AD0)
SPI_MOSI: U1.23 (PA7), U5.14 (AP_SDA/AP_SDIO/AP_SDI)
SPI_SCK: U1.21 (PA5), U5.13 (AP_SCL/AP_SCLK)
USART3_RX: J3.3, U1.30 (PB11)
USART3_TX: J3.2, U1.29 (PB10)
VBUS: D4.2 (A), USB1.2 (VBUS), USB1.11 (VBUS)

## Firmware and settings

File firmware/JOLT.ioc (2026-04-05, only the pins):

Mcu.UserName=STM32F405RGTx
PA11.Signal=USB_OTG_FS_DM
PA12.Signal=USB_OTG_FS_DP
PA13.Signal=SYS_JTMS-SWDIO
PA14.Signal=SYS_JTCK-SWCLK
PA2.Signal=USART2_TX
PA3.Signal=USART2_RX
PA5.Signal=SPI1_SCK
PA6.Signal=SPI1_MISO
PA7.Signal=SPI1_MOSI
PB0.Signal=GPIO_Output
PB1.Signal=GPIO_Input
PB10.Signal=USART3_TX
PB11.Signal=USART3_RX
PB2.Signal=GPIO_Input
PB6.Signal=I2C1_SCL
PB7.Signal=I2C1_SDA
PC13-ANTI_TAMP.GPIO_Label=STATUS_LED
PC13-ANTI_TAMP.Signal=GPIO_Output
PH0-OSC_IN.Signal=RCC_OSC_IN
PH1-OSC_OUT.Signal=RCC_OSC_OUT

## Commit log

2026-03-23 Add STEP files and update README.md
    [JOLT_Femur_LEFT.step, JOLT_Femur_RIGHT.step, JOLT_Tibia.step]
2026-03-24 Mark Hip bracket CAD as completed
2026-03-24 Add 3d files
    [JOLT_Femur.FCStd, JOLT_Femur_LEFT.FCStd, JOLT_Femur_LEFT.step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]
2026-03-25 Modify CAD project status in README
    Updated the status of the Body plate and added Chassis finalization.
2026-04-04 Add project files
    [Board_Power.kicad_sch, IMU.kicad_sch, JOLT_Femur.FCStd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]
2026-04-05 Add modified files
    [JOLT_V1.kicad_pcb]
2026-04-05 Add final files
    [Board_Power.kicad_sch, IMU.kicad_sch, JOLT_Femur.FCStd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]
2026-04-06 Add BOM
    [J.O.L.T (Joint Operated Legged Terrain-walker)-bom.csv]
2026-04-18 Add new files after review and update readme
    [J.O.L.T (Joint Operated Legged Terrain-walker)-bom.csv, JOLT_V1.kicad_pcb, bom.csv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]
2026-04-20 Update files
    [JOLT_V1.kicad_pcb]
2026-04-23 Update README and add updated files for printing
    [JOLT_Assembled.FCStd, JOLT_Chassis_Pin.3mf, JOLT_Chassis_Pin.FCStd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]
2026-04-23 Add error-fixed files
    [positions.csv]
2026-04-27 Add 4 layer pcb and update readme
    [JOLT_V1.kicad_pcb, positions.csv]
2026-05-06 Update to 2-layer pcb
    [positions.csv]
2026-05-06 Add updated kicad files
    [JOLT_V1.kicad_pcb]
2026-05-25 Update files for Forge
    [BOM.csv]
2026-06-02 Update Bill of Materials with cost adjustments
2026-06-24 Update Bill of Materials with new items and costs
